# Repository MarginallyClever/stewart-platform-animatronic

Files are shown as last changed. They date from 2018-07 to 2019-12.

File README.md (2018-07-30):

# stewart-platform-animatronic

https://www.instagram.com/p/BleN0-bjPU8/

These are the printed parts, PCB design files, and laser cutting plans for miniature stewart platforms used in animatronics.

There are four in the instagram link above.  To make ONE of these platforms you will need

6x M3 rod 10cm long
12x M3x10 screws (can be M3x15)
18x M3x15 screws
3x 3d printed lower gimbal limit
6x 3d printed servo horn 
6x 3d printed servo mount
1x 3d printed top
1x laser cut floor A
1x laser cut floor B

For the handle you'll need 3x M3x15 screws.

To fit the servo into the servo mount I unscrewed the back so the wire would bend down and out of the way.  This is convenient on the input side where I also removed one gear AND unsoldered the white wire and resoldered it to the potentiometer.

The potentiometer returns a value between ~110 and ~520 (of a possible 0-1023).  In the code I adjusted the floor and ceiling values to get the full range of motion out of the servos.

To attach the arms to the input servos, I opened the serial window and turned the servo until it was in middle position, then attached the arm horizontally.  The output servos could then be attached to match.  If there's a better way to do this, please let me know.

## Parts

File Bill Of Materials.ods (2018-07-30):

ONE STEWART PLATFORM
Method | Qty | Part
3D print | 6 | servo horn
3D print | 1 | top
3D print | 6 | servo mount
3D print | 3 | lower gimbal limit
3D print | 1 | handle
buy | 6 | servo 180 degree plastic gear s3003
buy | 12 | ball joint
buy | 12 | m3x14 socket head cap screw 91290A120
Buy & make | 6 | m3 rod, 10cm long
laser cut | 1 | floor plate
Buy 1m m3 rod and cut into 6 pieces.
Very likely the ends will need to be filed. I use an angle grinder.
This also means cut the rods longer than you need.
The second stewart platform will require that you open the servos, disconnect the motor, and solder the PWM wire to the potentiometer.
BRAIN
Method | Qty | Part
buy | 1 | PCB
buy | 3 | 40 pin breakaway male headers
buy | 1 | Arduino UNO or equivalent
buy | 1 | 5v4a power supply
buy | 1 | 2 pin 5.08” screw terminal block
extra servo attachment points have been added for future proofing.
maybe you want to add extra features on the output stewart platform.

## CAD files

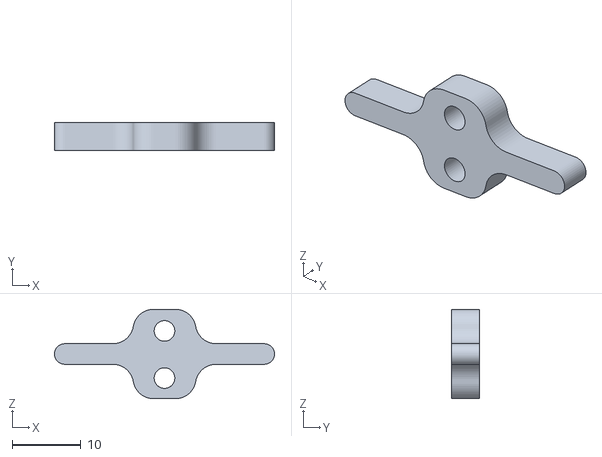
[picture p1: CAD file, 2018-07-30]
3D printed parts/lower gimbal limit.stl
32.0 x 4.00 x 13.0

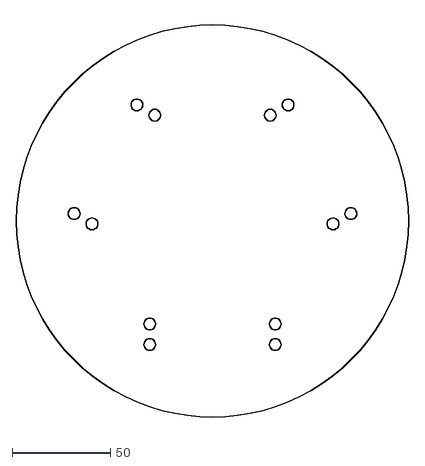
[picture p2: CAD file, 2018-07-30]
laser cut floor B.dxf
200.0 x 208.9

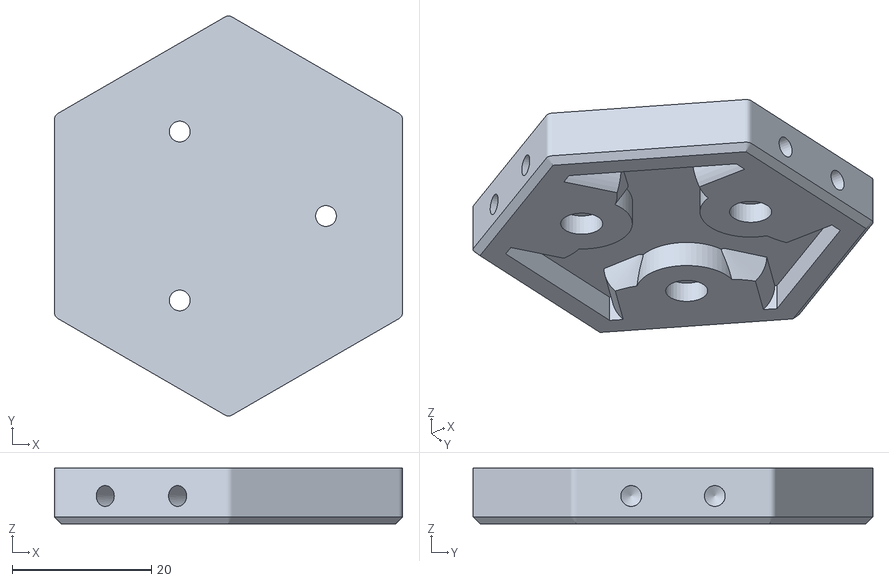
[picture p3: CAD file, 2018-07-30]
3D printed parts/top v2.stl
50.0 x 57.4 x 8.00

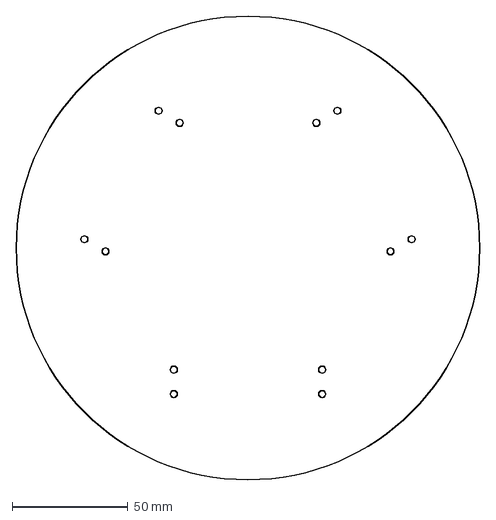
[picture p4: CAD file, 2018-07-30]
laser cut floor A.dxf
200.0 x 200.0 mm

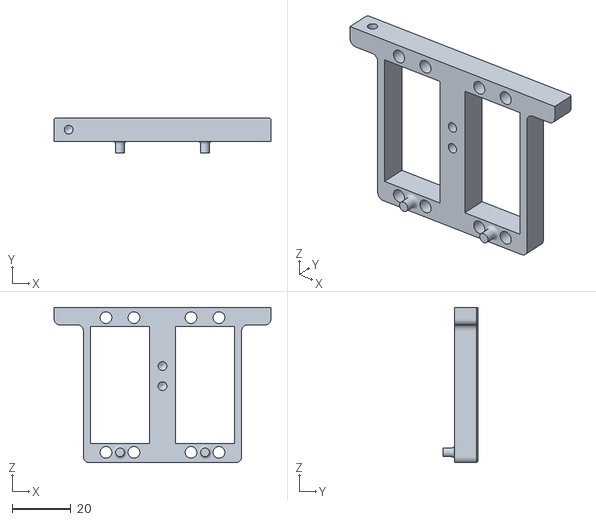
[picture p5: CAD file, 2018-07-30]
3D printed parts/servo mount.stl
74.0 x 12.0 x 53.0

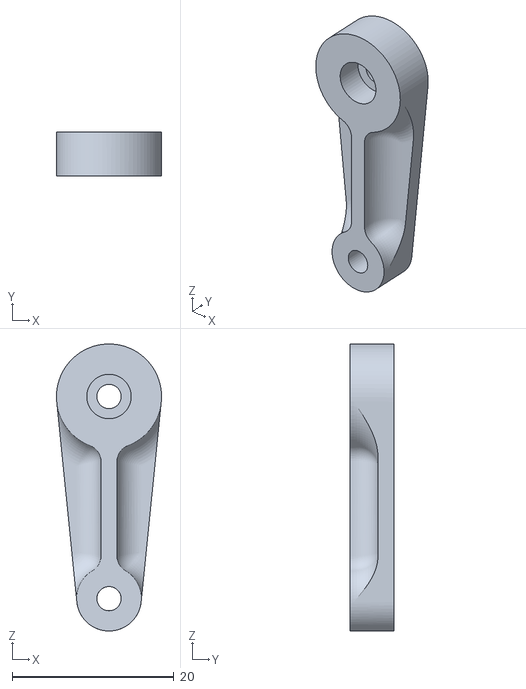
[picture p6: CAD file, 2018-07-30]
3D printed parts/servo horn.stl
13.0 x 5.50 x 35.5

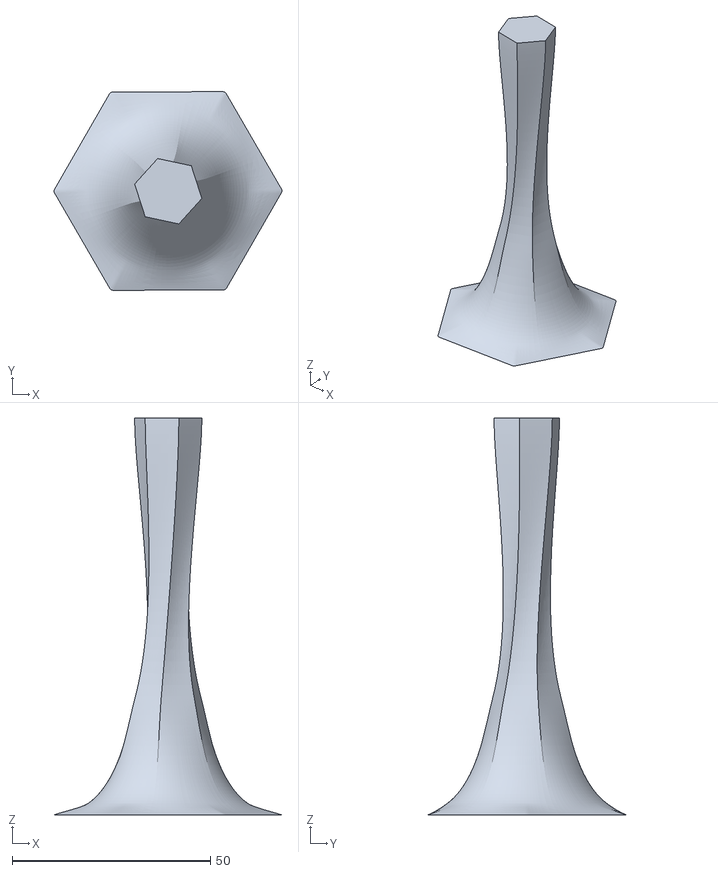
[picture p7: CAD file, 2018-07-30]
3D printed parts/handle.stl
57.4 x 50.0 x 100.0

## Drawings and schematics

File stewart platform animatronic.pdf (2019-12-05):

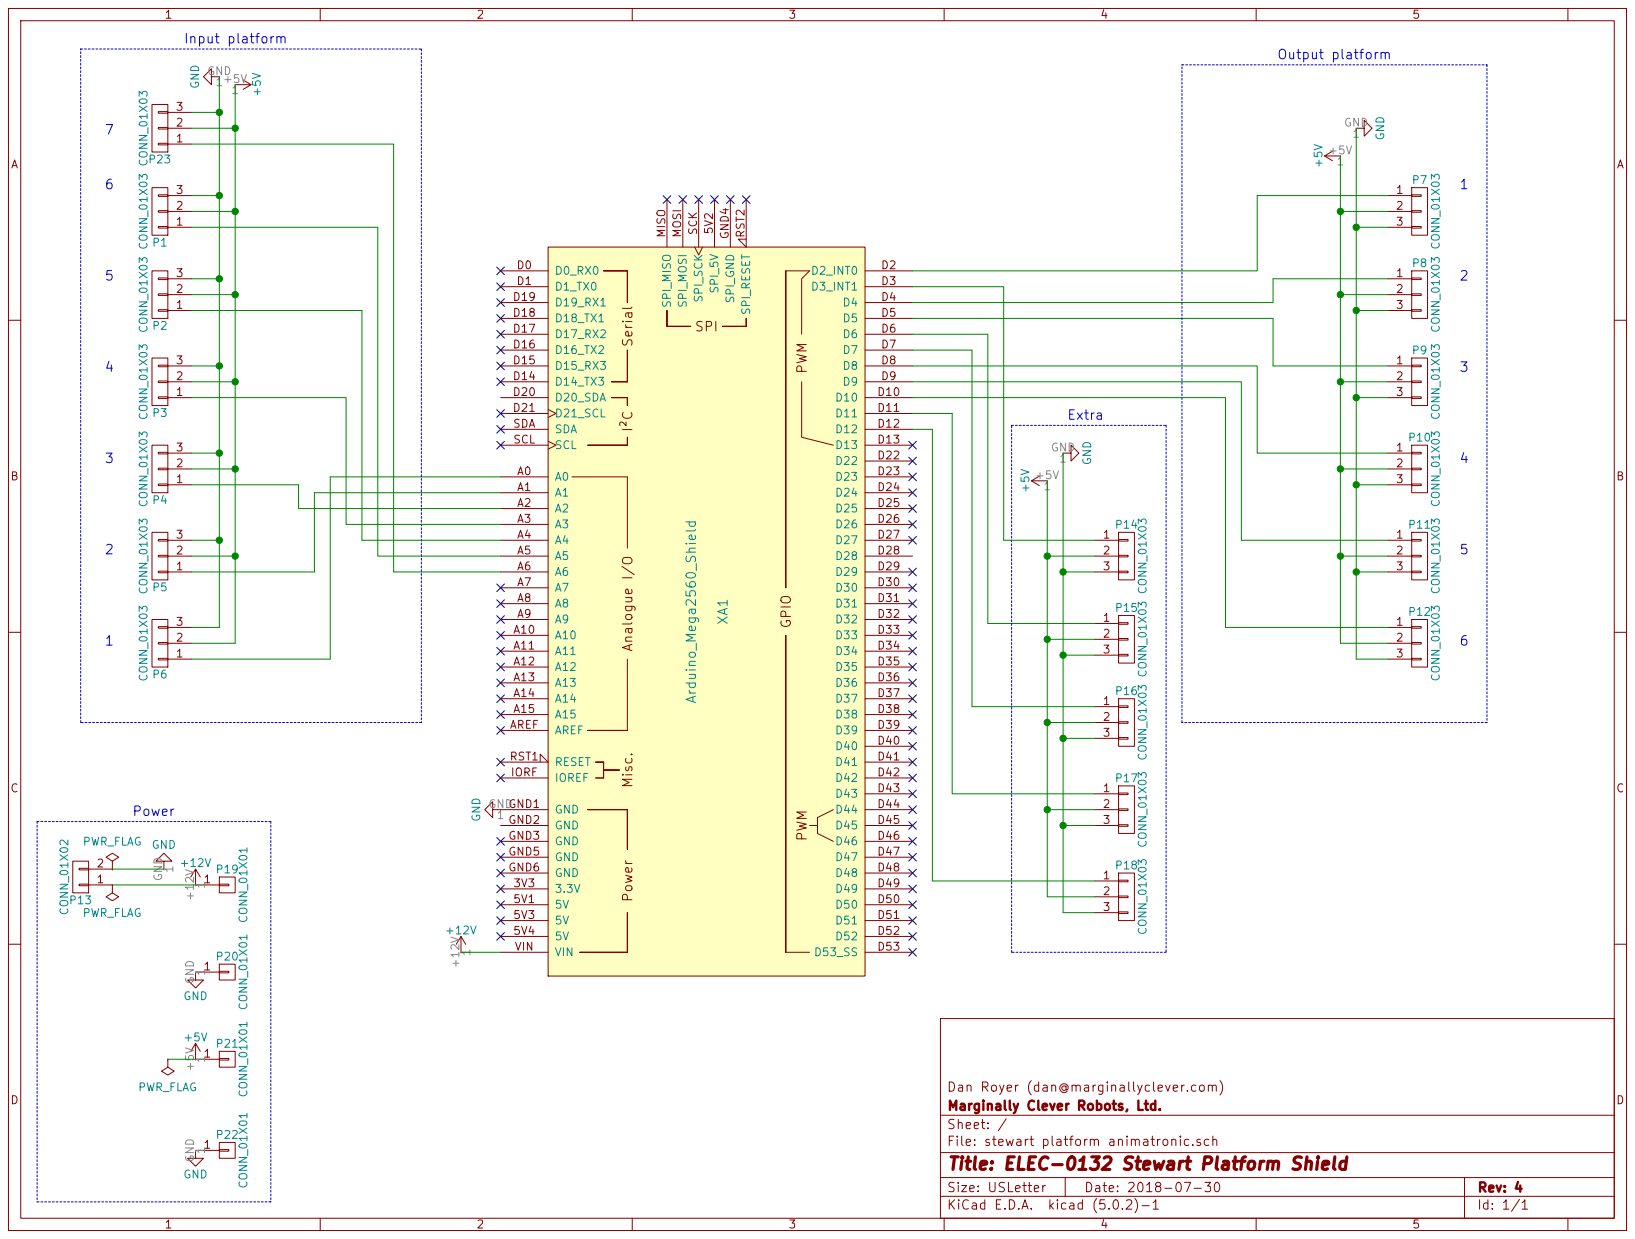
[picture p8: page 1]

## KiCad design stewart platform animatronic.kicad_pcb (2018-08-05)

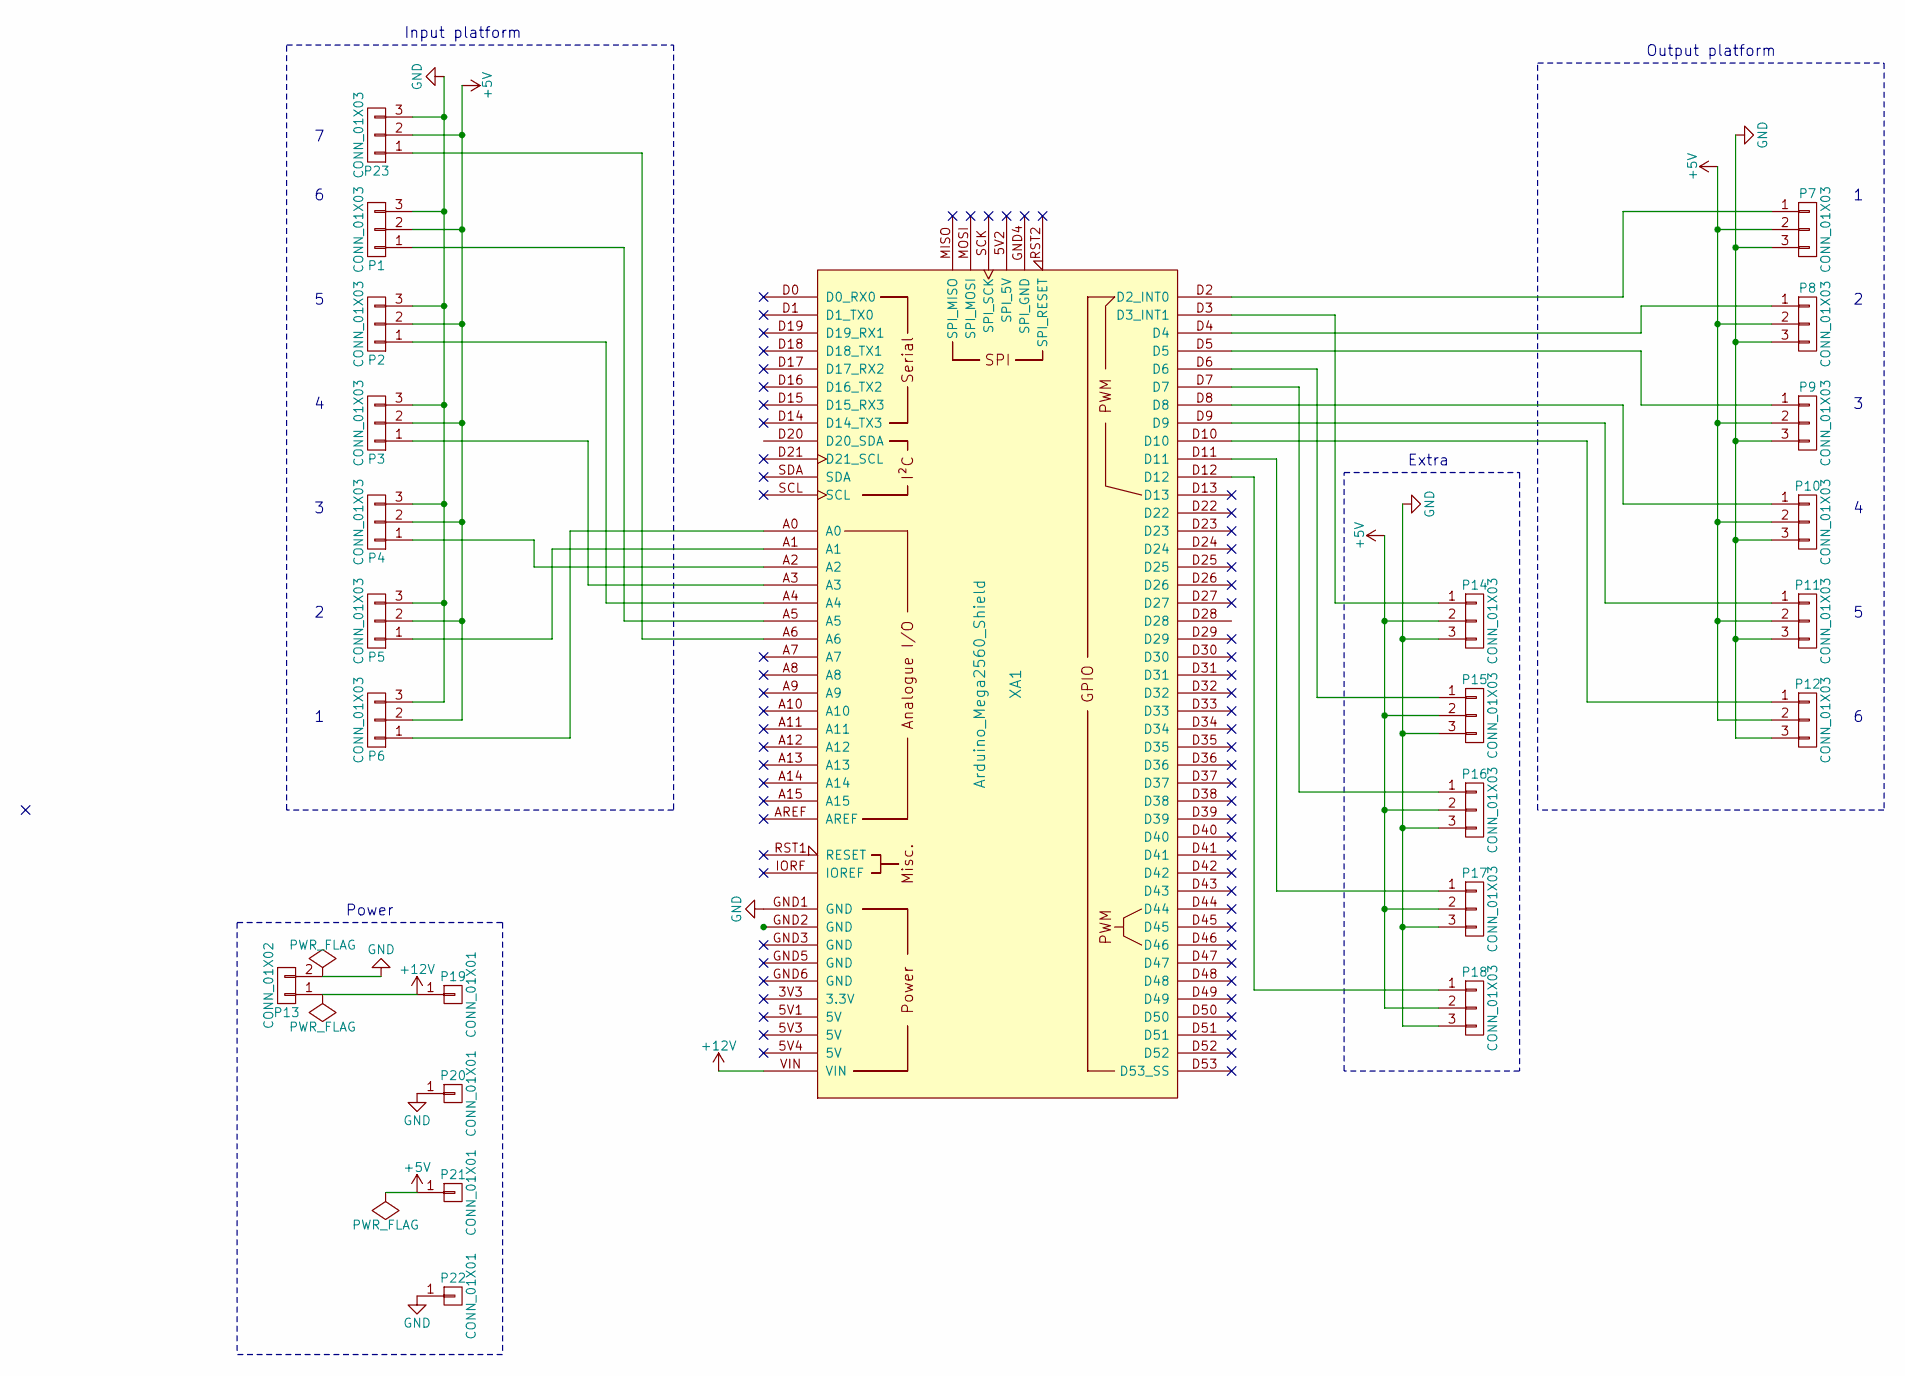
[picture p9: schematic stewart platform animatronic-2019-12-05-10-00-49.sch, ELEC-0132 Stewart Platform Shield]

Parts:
P1, P2, P3, P4, P5, P6, P7, P8, P9, P10, P11, P12, P14, P15, P16, P17, P18, P23: CONN_01X03; Socket_Strip_Straight_1x03_Pitch2.54mm
P13: CONN_01X02; TerminalBlock_bornier-2_P5.08mm
P19, P20, P21, P22: CONN_01X01; Socket_Strip_Straight_1x01_Pitch2.54mm
XA1: Arduino_Mega2560_Shield

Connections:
+5V: P1.2, P2.2, P3.2, P4.2, P5.2, P6.2, P7.2, P8.2, P9.2, P10.2, P11.2, P12.2, P14.2, P15.2, P16.2, P17.2, P18.2, P21.1, P23.2
+12V: P13.1, P19.1, XA1.VIN
GND: P1.3, P2.3, P3.3, P4.3, P5.3, P6.3, P7.3, P8.3, P9.3, P10.3, P11.3, P12.3, P13.2, P14.3, P15.3, P16.3, P17.3, P18.3, P20.1, P22.1, P23.3, XA1.GND1 (GND)
unnamed: P1.1, XA1.A5
unnamed: P2.1, XA1.A4
unnamed: P3.1, XA1.A3
unnamed: P4.1, XA1.A2
unnamed: P5.1, XA1.A1
unnamed: P6.1, XA1.A0
unnamed: P7.1, XA1.D2 (D2_INT0)
unnamed: P8.1, XA1.D4
unnamed: P9.1, XA1.D5
unnamed: P10.1, XA1.D8
unnamed: P11.1, XA1.D9
unnamed: P12.1, XA1.D10
unnamed: P14.1, XA1.D3 (D3_INT1)
unnamed: P15.1, XA1.D6
unnamed: P16.1, XA1.D7
unnamed: P17.1, XA1.D11
unnamed: P18.1, XA1.D12
unnamed: P23.1, XA1.A6

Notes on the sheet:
Input platform
Output platform
Power
Extra
1 2 3 4 5 6
6 5 4 3 2 1

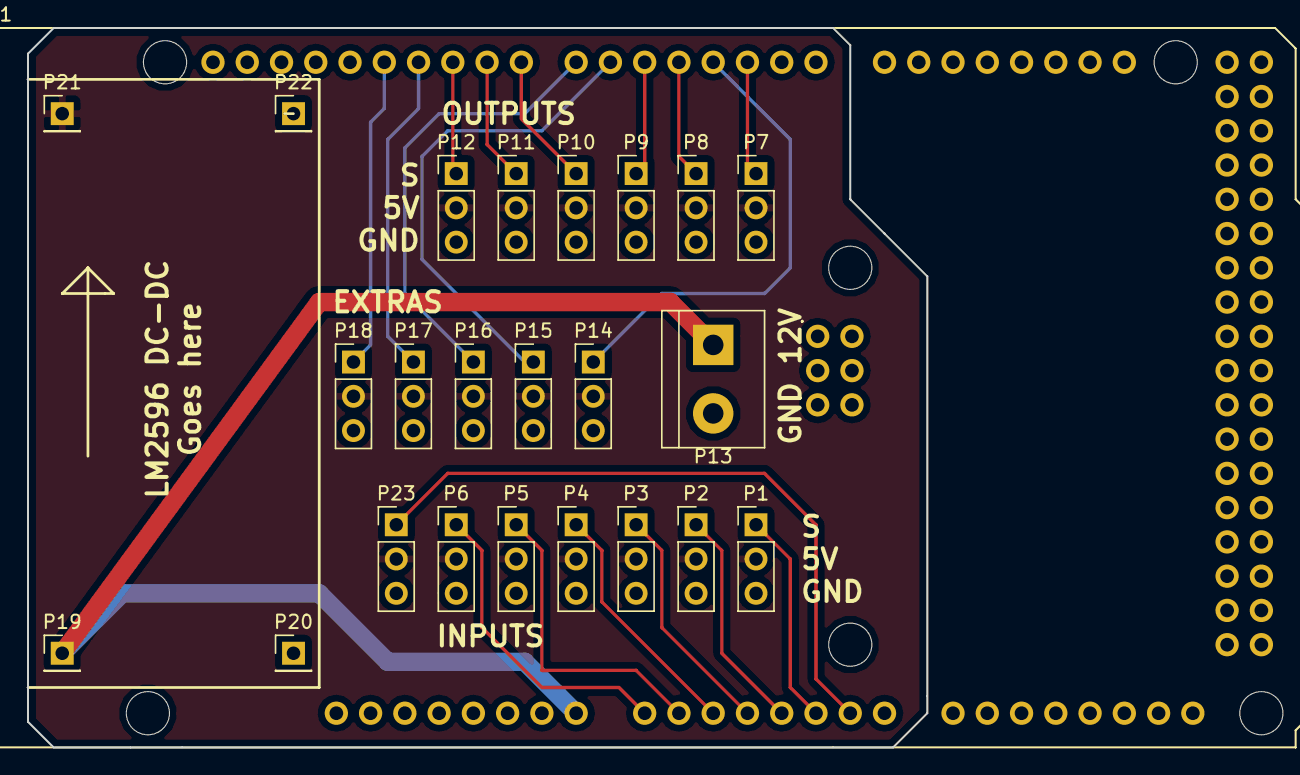
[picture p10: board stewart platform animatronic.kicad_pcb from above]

Board: 2 copper layers, 66.7 x 53.3 mm, 24 parts (0 on the bottom side), 21 nets.

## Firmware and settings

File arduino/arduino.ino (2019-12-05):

#include <Servo.h>

#define NUM_SERVOS  7

// minimum/maximum values read via serial.  customized per-servo.
// these numbers were tested on a 5v3a power supply and may change with a 5v4a supply.
int floors  [NUM_SERVOS] = { 0, 0, 0, 0, 0, 0, 0 };
int ceilings[NUM_SERVOS] = { 670, 670, 670, 670, 670, 670, 670, };
int outputPins[NUM_SERVOS] = { 2, 4, 5, 8, 9, 10, 3 };




Servo a[NUM_SERVOS];

void setup() {
  Serial.begin(57600);
  Serial.println("\n** SETUP **");

  for(int i=0;i<NUM_SERVOS;++i) {
    a[i].attach(outputPins[i]);
  }

  Serial.println("\n** LOOP **");
}

void loop() {
  for(int i=0;i<NUM_SERVOS;++i) {
    int j = analogRead(i);
    float f = map(j,floors[i],ceilings[i],10,170);
    //float f = (float)j * 180.0/1024.0;
    Serial.print(j);
    Serial.print('=');
    Serial.print(f);
    Serial.print('\t');
    a[i].write(f);
  }
  Serial.print("\n");

  delay(5);
}

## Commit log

2018-07-30 updated README, laser cut plans
    [laser cut floor A.dxf, laser cut floor B.dxf]
2018-07-30 mega2560 version
    [stewart platform animatronic.sch]
2018-08-05 updated PCB for MEGA
    for MEGA design
    [stewart platform animatronic.kicad_pcb, stewart platform animatronic.sch]
2019-12-05 updated kicad version
    [stewart platform animatronic-2019-12-05-10-00-49.sch]
